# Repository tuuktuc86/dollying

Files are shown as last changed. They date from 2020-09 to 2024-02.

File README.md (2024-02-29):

# Dollying (휴대폰 어플리케이션과 연동 가능한 영상 촬영 장비)

## 작품개요
### 개발배경
대한민국 기준, 하루 평균 유튜브 시청 시간은 58.8분으로 다른 프로그램에 비해 사용 시간면에서 월등히 높다. 유튜브 영상 수요의 증가로 유튜브 영상 업로드 시간이 5년 사이에 약 10배 증가하였으며, 업로드 되는 영상 중 42%는 People 카테고리로 Vlog와 같은 개인의 일상에 관련되는 내용을 담고 있다. 이러한 1인 영상 매체가 성장하며 개인 방송장비 매출도 2년 사이에 540% 증가하였다.

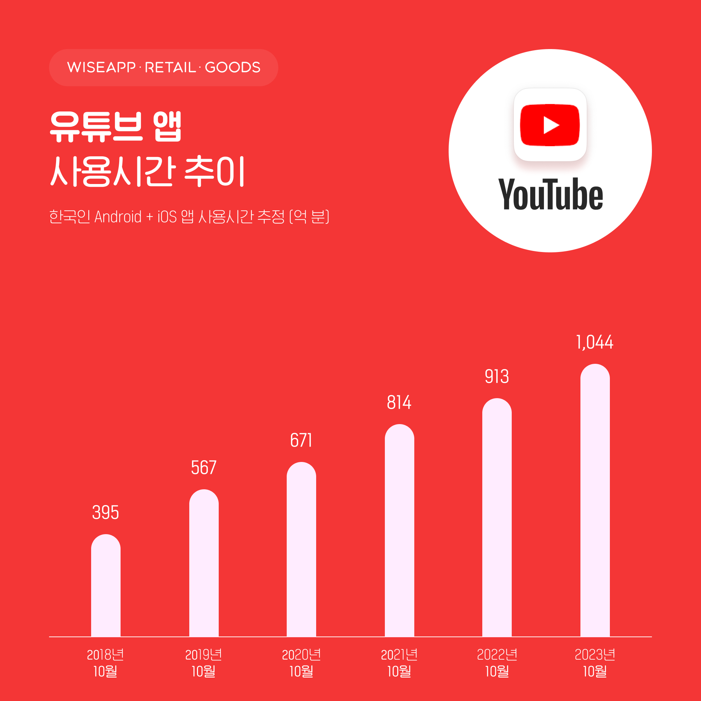
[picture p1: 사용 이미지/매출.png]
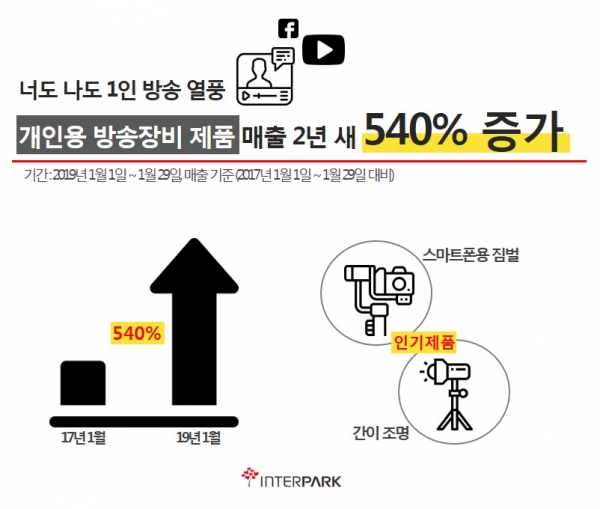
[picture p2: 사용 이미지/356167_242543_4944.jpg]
 

### 전동달리
영화 촬영 시 사용하는 장비를 최근 소형화, 전동화 시켜서 1인 영상 촬영에 사용되고 있다. 현재 시중에 사용되는 제품은 움직임 설정에 정교함이 없기 때문에 휴대폰 어플을 통해서 섬세한 제어와 다양한 움직임을 가능하게 하는 전동달리 제작을 목표로 하였다.

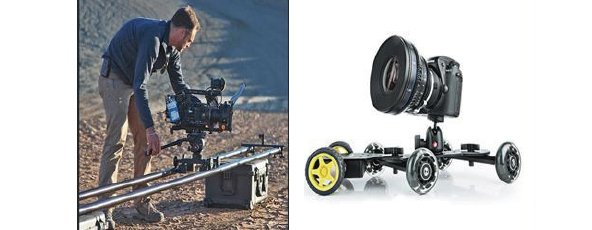
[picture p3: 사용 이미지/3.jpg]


## 작품 설명
### 주요 동작 및 특징
외관
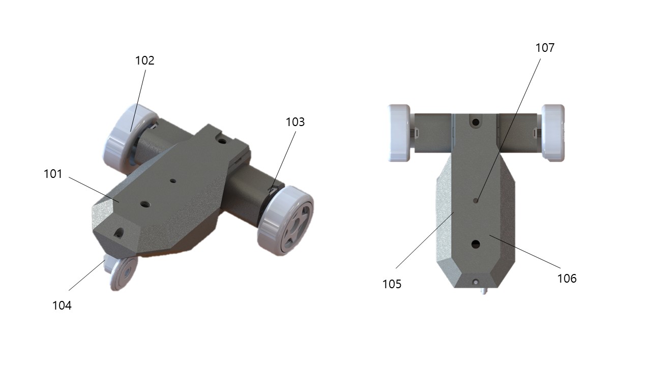
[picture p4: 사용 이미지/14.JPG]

- 앞바퀴는 방향을, 뒷바퀴는 전진과 후진 기능을 수행한다.<br/>
- 윗면의 구멍으로 카메라를 고정한다.<br/>

애플리케이션 설명 : UI 디자인
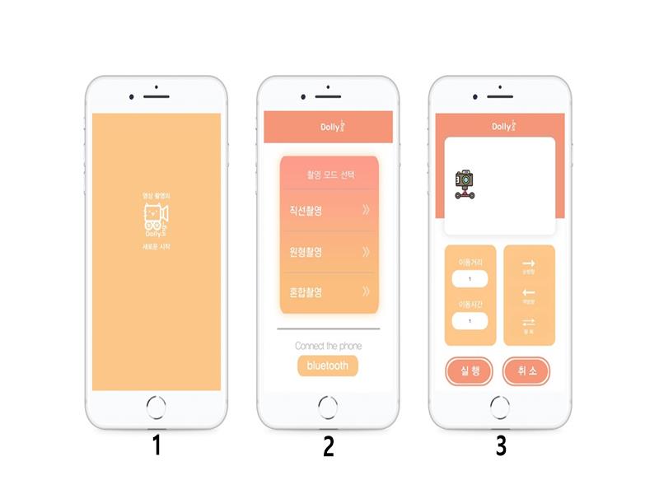
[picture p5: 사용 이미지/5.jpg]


1. 애플리케이션 시작 화면이다.<br/>
2. 메뉴화면으로 블루투스 연결과 모드선택(직선 촬영, 원형 촬영, 혼합 촬영)이 가능하다.<br/>
3. 직선 촬영 모드 > 이동거리와 이동시간을 입력할 수 있고 기능(순방향, 역방향, 왕복)을 설정이 가능하다<br/>
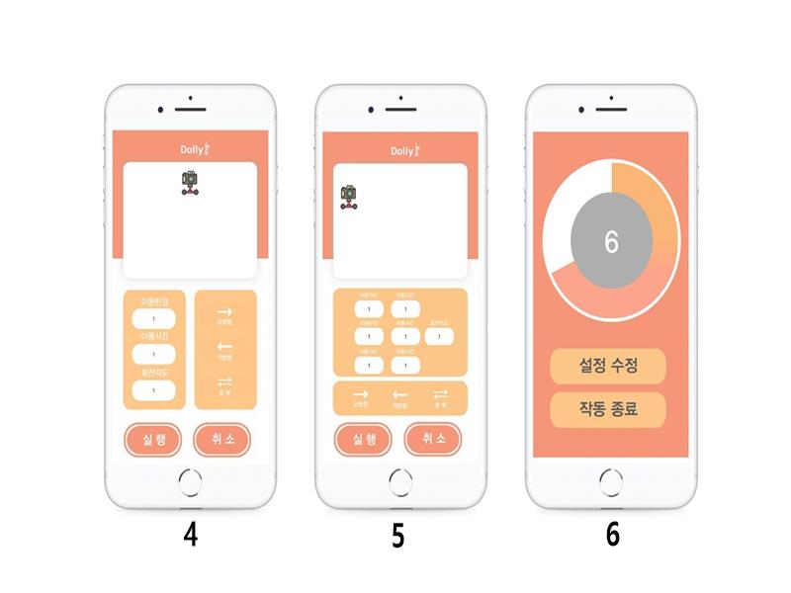
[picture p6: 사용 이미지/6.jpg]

4. 원형 촬영 모드 > 이동반경, 이동시간, 회전각도를 입력 할 수 있고 기능(순방향, 역방향, 왕복)을 설정 가능, 이동반경은 회전 반지름을, 회전각도는 원형으로 회전하는 각도를 의미한다.<br/>
5. 혼합 촬영 모드 > 직선촬영모드와 원형 촬영 모드를 합친 모드로 직선운동1-원형운동-직선운동2 구조로 구성, 직선운동 1,2구간의 이동거리와 이동시간과 원형운동의 이동반경, 이동시간, 회전 각도를 입력 할 수 있다. 또한 기능(순방향, 역방향, 왕복)을 설정이 가능하다.<br/>
6. 각 모드에서 실행을 눌렀을 때 넘어가는 화면. 기기 작동 시간이 종료되는 시간을 나타내며 입력 값은 수정이 가능하다.<br/>

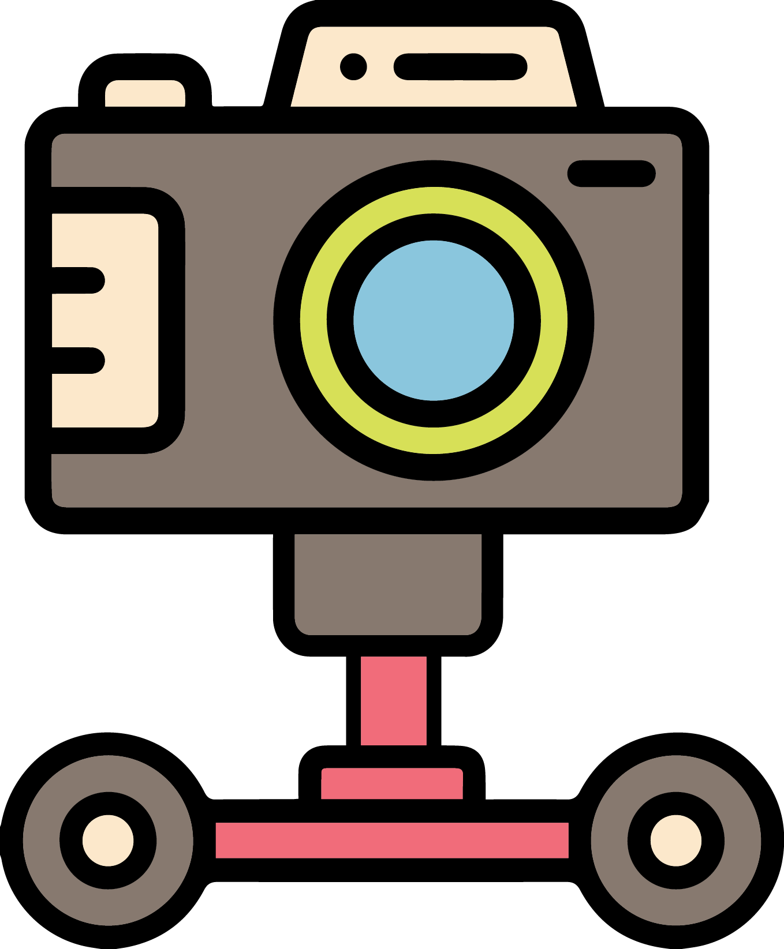
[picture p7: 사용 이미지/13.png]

③,④,⑤번 상단의 전동 달리 그림은 설정 값에 따라 움직이며 사용자가 기기 실행 전 움직임을 알 수 있도록 도와준다.<br/>
⑥번 상단의 숫자는 기기가 움직이는데 걸리는 시간을 알려주며 시간이 지나면서 감소한다.<br/>

### 전체 시스템 구성
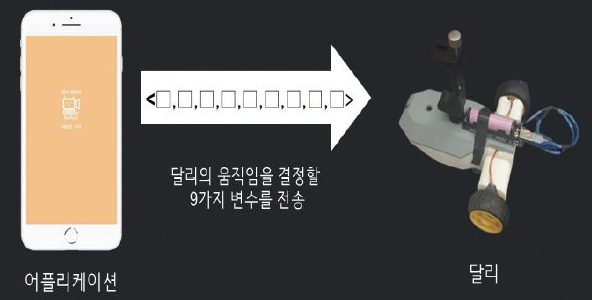
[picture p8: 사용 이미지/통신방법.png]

<> 전송의 시작과 끝을 나타내는 구분자  <br/>
① 촬영 모드(직선 촬영, 원형 촬영, 혼합 촬영)를 결정하는 변수  <br/>
② 직선 촬영 모드 시 이동거리 변수, 혼합 촬영 모드 시 직선운동 1구간의 이동거리 변수 <br/> 
③ 직선 촬영 모드 시 이동시간 변수, 혼합 촬영 모드 시 직선운동 1구간의 이동시간 변수  <br/>
④ 원형 촬영 모드 시 이동반경 변수, 혼합 촬영 모드 시 원형운동의 이동반경 변수  <br/>
⑤ 원형 촬영 모드 시 이동시간 변수, 혼합 촬영 모드 시 원형운동의 이동시간 변수  <br/>
⑥ 원형 촬영 모드 시 회전각도 변수, 혼합촬영모드 시 원형운동의 회전각도 변수  <br/>
⑦ 혼합 촬영 모드 시 직선운동 2구간의 이동거리 변수  <br/>
⑧ 혼합 촬영 모드 시 직선운동 2구간의 이동시간 변수  <br/>
⑨ 기능(순방향, 역방향, 왕복)을 나타내는 변수  <br/>

### 개발 환경(개발 언어, Tool, 사용 시스템 등)
전동 달리 코딩 : C,C++, Arduiono<br/>
애플리케이션 개발 : C#, Unity<br/>
전동 달리 모델링 : SOLIDWORKS<br/>
어플, 로고 디자인 : Adobe Photoshop,Adobe Illustrator<br/>

## 단계별 제작 과정
·  0 단계: 아이디어 선정<br/>
·  1 단계: UI디자인 구성, 전동달리 구조 확정, 사용 부품 선정<br/>
·  2 단계: 전동달리 코딩 개발, 애플리케이션 개발, 전동달리 모델링 및 3D프린터 출력<br/>
·  3 단계: 3D프린터 파트 조립, 기기 시험 작동 후 코드 수정<br/>

### 0단계 : 아이디어 선정
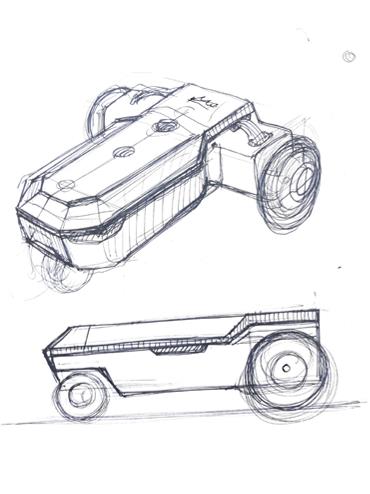
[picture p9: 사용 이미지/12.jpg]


### 1단계 : 어플 디자인 및 부품 구성
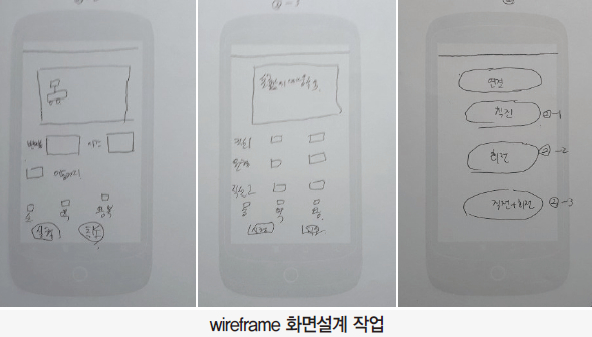
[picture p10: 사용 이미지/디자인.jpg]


사용부품 선정
· 아두이노 우노 x 1ea
· 아두이노 우노 쉴드 x 1ea
· 스텝모터, 모터 드라이버 x 2ea
· 서보모터 x 1ea
· 배터리 x 1ea
· 배터리 충전 모듈 x 1ea
· 바퀴 x 2ea

### 2단계 : 전동달리 모델링 및 3D프린터 출력


전동달리 코드 개발 : github 참고
어플리케이션 개발 : github 참고

### 3단계 : 3D프린터 파트 조립
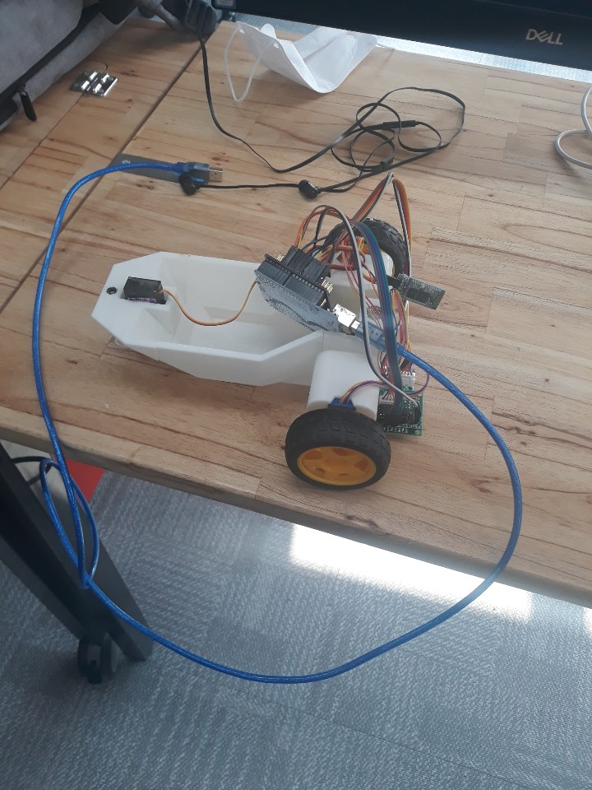
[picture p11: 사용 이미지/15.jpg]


기기 시험 작동 후 코드 수정
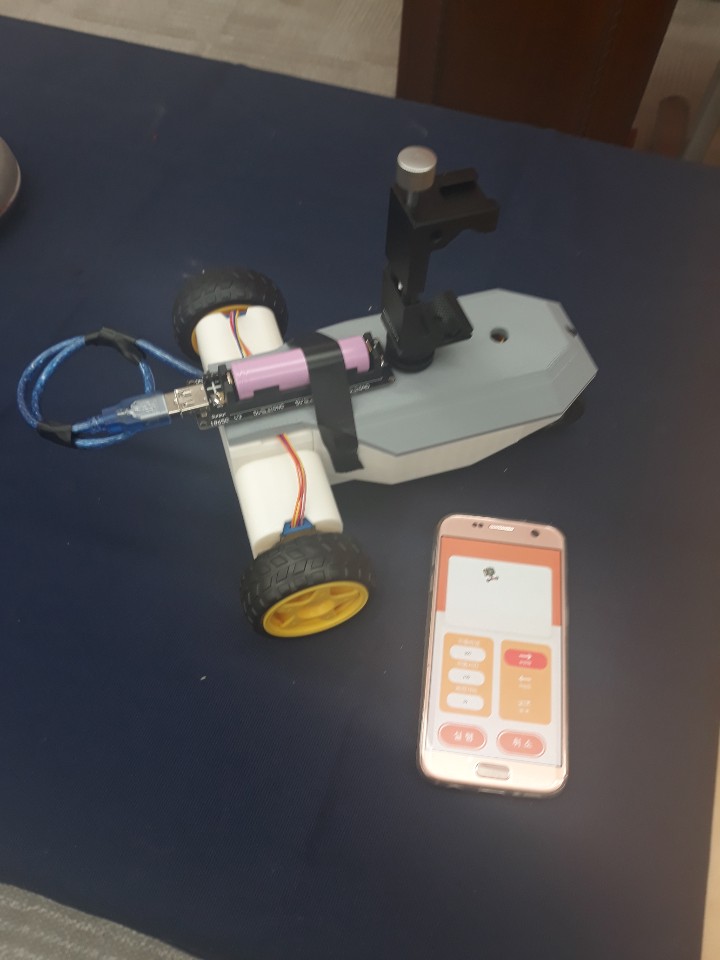
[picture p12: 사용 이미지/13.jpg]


## 기타

### 회로도
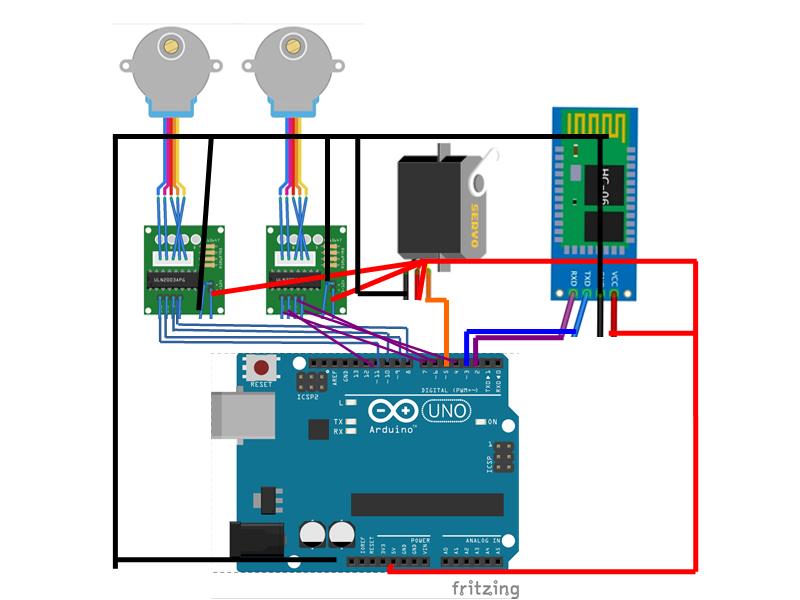
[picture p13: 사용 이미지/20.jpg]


### 플레이스토어 등록
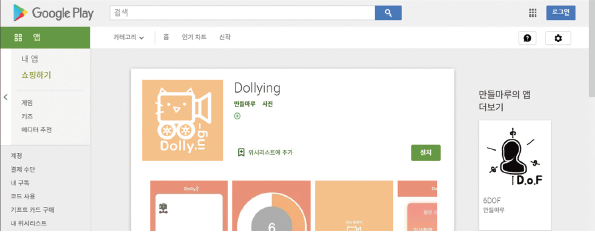
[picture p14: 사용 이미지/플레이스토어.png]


### 계산 과정
스텝 모터가 움직이는 데 필요한 값 계산
계산을 시작하기 전에 알아야 하는 값

1. 스텝모터가 1회전이 몇 개의 스텝으로 이루어져 있는지 여부
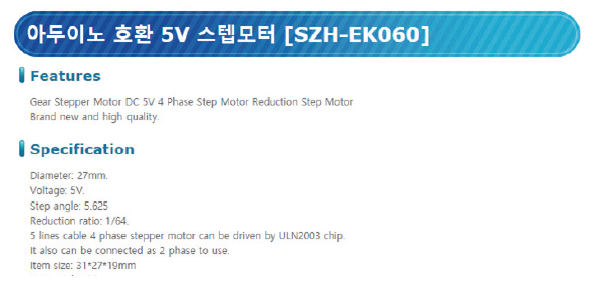
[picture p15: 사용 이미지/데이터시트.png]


2. 바퀴 반지름.
· 왼쪽 모터의 1회전에 필요한 스텝은 8이다.
· 디바이스마트에 나와있는 스텝모터 (SZH-EK060) 사양

Step angle이 5.425。이고 감속비는 1/64이므로 1스텝 0.084765625。당 회전한다. 360÷0.084765625 ≒4247이지만 모터드라이버의 full step모드에서는 1/2한 근사치인 2048을 이용한다.

애플리케이션에서 전송받는 값
1. 기기의 이동거리, 2. 기기 이동에 걸리는 시간

구해야 하는 값
1. 스텝모터의 회전속도는 rpm단위이기 때문에 위의 값들을 활용하여 rpm값을 구해야 한다.
2. 해당 거리만큼 이동하는 데 필요한 스텝 수를 알아야 한다.

회전에 필요한 스텝 수 구하기
1. 바퀴의 원주를 알아야 하므로 2πr(r은 반지름)을 통해서 원주를 알아낸다.
2. 이동 거리를 원주로 나누어 바퀴의 회전수를 구한다.
3. 회전수에 스텝 모터 한바퀴 스텝을 곱하여(이번 프로젝트에 사용한 스텝모터의 1회전에 필요한 스텝은 2048) 이동에 필요한 스텝을 알 수 있다.

회전속도 구하기
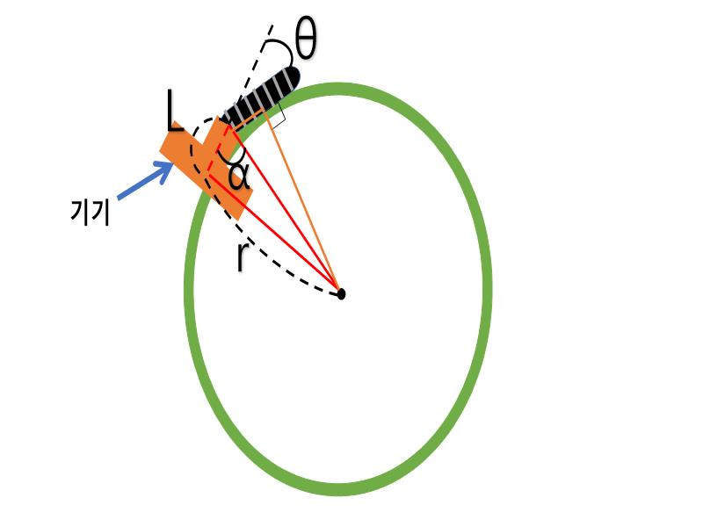
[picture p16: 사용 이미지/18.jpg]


1. rpm = 회전수 * 이동시간 / 60.

2. 회전 반지름에 따른 회전 각도 구하기
r= 회전 반지름
L= 기기 길이
α=  arctan(r/L)

빨간 삼각형과 주황 삼각형은 합동이므로 θ=180-2α이다.


http://www.ntrexgo.com/archives/39953

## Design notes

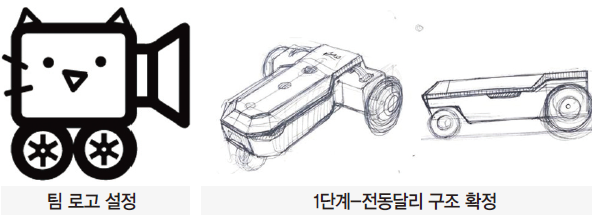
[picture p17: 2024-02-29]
사용 이미지/디자인2.png

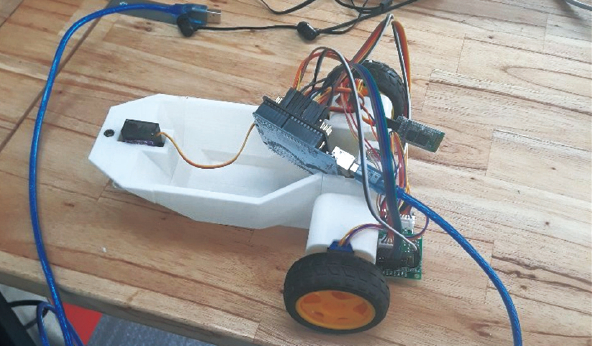
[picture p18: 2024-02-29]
사용 이미지/사진2.jpg

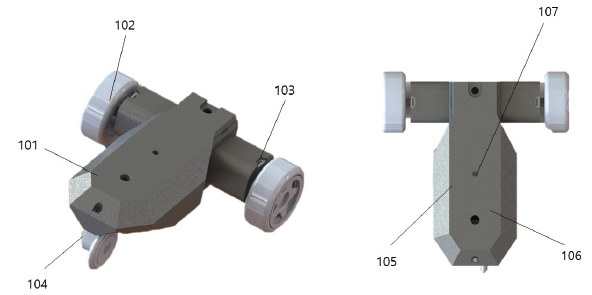
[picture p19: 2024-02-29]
사용 이미지/외형.jpg

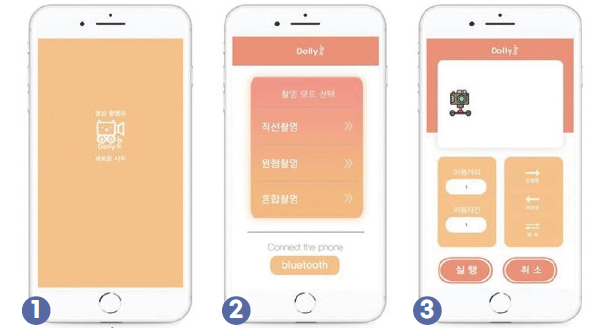
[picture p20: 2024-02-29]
사용 이미지/어플2.png

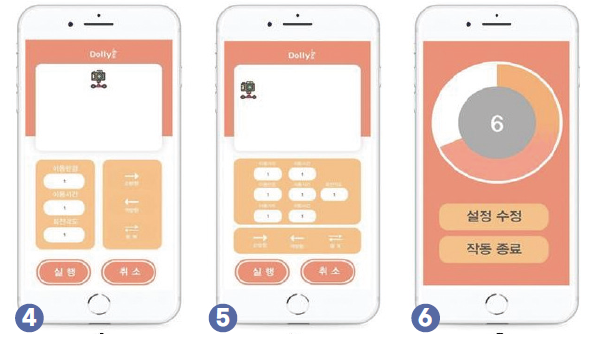
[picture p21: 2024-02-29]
사용 이미지/어플1.png

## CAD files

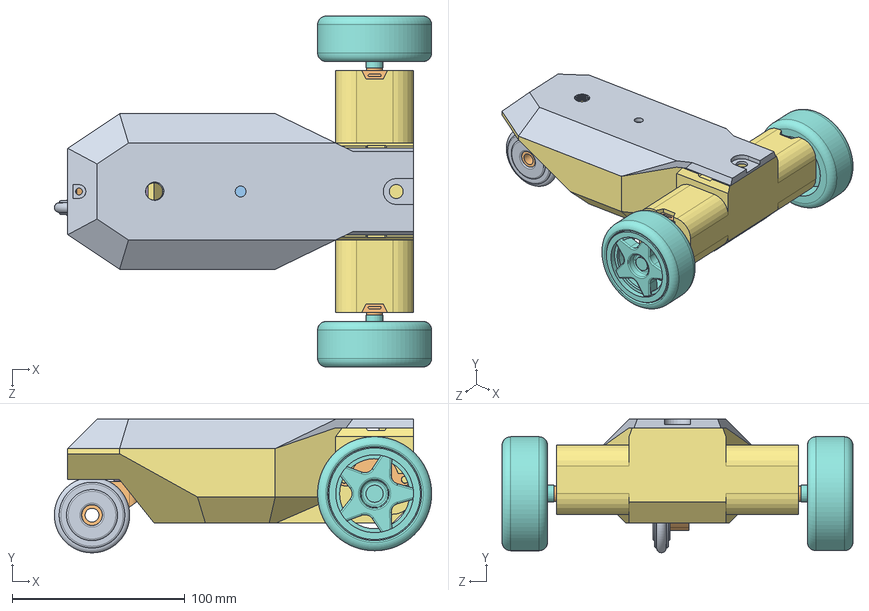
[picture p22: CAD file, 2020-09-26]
어셈블리1.SLDASM
218.2 x 77.3 x 203.0 mm
상단
바퀴모터 x 2
아두이노
건전지
모터드라이버 x 2
서보(조향)
하단
뒷바퀴 x 2
앞바꾸2
조향

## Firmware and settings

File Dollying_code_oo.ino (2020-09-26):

//헤더파일
#include <Servo.h>
#include <SoftwareSerial.h>
#include <Stepper.h>

//스테핑모터 정보. 모터 스펙에 맞게 설정
const int stepsPerRevolution = 2048; //28BYJ-48는 1회전당 2048스텝

//핀번호
#define BT_RXD 2
#define BT_TXD 3
Stepper rightStepper(stepsPerRevolution, 11, 9, 10, 8);  //오른쪽 바퀴를 돌릴 모터
Stepper leftStepper(stepsPerRevolution, 7, 12, 6, 4);    //왼쪽 바퀴를 돌릴 모터
int servoPin = 5;                                        // PWM 핀인 ~표시가 있는 핀에 연결


//블루투스 설정
SoftwareSerial BTSerial(BT_RXD, BT_TXD); // change this to fit the number of steps per revolution

//data 읽기 시작, 종료 상태 변수
bool isStart = false;   // 읽기 시작
bool isEnd = false;     // 읽기 종료
String resultStr = "";  // 최종 Data를 저장할 문자열

//불루투스에서 받은 값을 나눠서 넣을 값.
int sep = 0;            //직선, 원형, 혼합 운동을 결정하는 변수
int dis1 = 0;           //직선 운동의 거리 변수, 혼합 운동의 1번 직선 구간 거리 변수
int tim1 = 0;           //직선 운동의 시간 변수, 혼합 운동의 1번 직선 구간 시간 변수
int rad2 = 0;           //원형 운동의 반지름 변수, 혼합 운동의 회전 구간의 반지름 변수
int tim2 = 0;           //원형 운동의 시간 변수, 혼합 운동의 회전 구간의 시간 변수
int ang2 = 0;           //원형 운동의 각도 변수, 혼합 운동의 회전 구간의 각도 변수
int dis3 = 0;           //혼합 운동의 2번 직선 구간 거리 변수
int tim3 = 0;           //혼합 운동의 2번 직선 구간 시간 변수
int mod = 0;            //직진, 후진, 왕복 기능을 결정하는 변수

//서브모터 설정
Servo servo;           // Servo 클래스로 servo 객체 생성
int angle = 0;         // Servo 모터의 각도 (0~180)
int stAngle = 82;      //Servo 모터 직진용 각도, 82도가 직진, 사용하기 전에 기기마다 맞는 설정값을 입력해줘야 함
double ccAngle = 0;    // 원형 운동시 서브모터 각도, 어플에서 넘어온 값으로 변경됨
int tnAngle = 0;       // 혼합 운동시 서브모터 각도, 어플에서 넘어온 값으로 변경됨

//바퀴 데이터
int wheelRadius = 3;                            //바퀴 반지름
float wheelCircum = wheelRadius * 2 * 3.141592; // 바퀴 원주


//직선 운동시 필요 데이터를 계산하기 위한 변수
float stTurnNum = 0;              //회전수
float stStepPerRevolution = 0;    //step per revolution
float stSpeedNeed = 0;            //회전속도(rpm)을 구하기 위해 필요한 변수
float stStepSpeed = 0;            //회전속도(rpm)

//원형 운동시 필요 데이터를 계산하기 위한 변수
float ccTurnNum = 0;            //회전수
float ccDis = 0;                //회전 이동거리
float ccStepPerRevolution = 0;  //step per revolution
float ccSpeedNeed = 0;          //회전속도(rpm)을 구하기 위해 필요한 변수
float ccStepSpeed = 0;          //회전속도(rpm)

//직선 운동3에 필요한 데이터를 계산하기 위한 변수
int stTurnNum3 = 0;             //회전수
int stStepPerRevolution3 = 0;   //step per revolution
int stSpeedNeed3 = 0;           //회전속도(rpm)을 구하기 위해 필요한 변수
int stStepSpeed3 = 0;           //회전속도(rpm)

//몸체 데이터
float bodylength = 10; // 몸체 세로 길이. 회전각을 구할 때에 필요

//,를 찾아내기 위한 변수
int first = 0;
int second = 0;
int third = 0;
int fourth = 0;
int fifth = 0;
int sixth = 0;
int seventh = 0;
int eighth = 0;

//회전에 필요한 데이터
int turnAngle = 0;
float turnData = 0;

void setup() {
  //통신 설정
  Serial.begin(9600);     //컴퓨터와의 통신속도 설정
  BTSerial.begin(9600);   //블루투스와의 통신속도 설정

  //Servo 모터 핀 설정
  servo.attach(servoPin); //servoPin 데이터는 위에 표기
}

void loop() {

  if (BTSerial.available()) {
    while (1) {
      char val = BTSerial.read();   //블루투스 데이터를 받아와 val변수에 삽입

      //데이터 읽기 시작
      if (val == '<') {
        Serial.println("start");
        resultStr = ""; // 최종 Data 문자열 초기화
        isStart = true;
        isEnd = false;
        continue;   // while문으로 바로 이동
      }
      // 데이터 읽기 종료
      else if (val == '>') {
        Serial.println("end");
        isEnd = true;
        break;
      }
      // 중간 데이터값을 최종 Data 문자열에 추가
      else {
        resultStr = String(resultStr + val);
      }
    }

    //시작 부호와 종료 부호가 들어왔다면
    if (isStart == true && isEnd == true) {
      Serial.print("전송된 데이터 : ");
      Serial.println(resultStr);

      //컴마 기호 파악
      first = resultStr.indexOf(",");
      second = resultStr.indexOf(",", first + 1);
      third = resultStr.indexOf(",", second + 1);
      fourth = resultStr.indexOf(",", third + 1);
      fifth = resultStr.indexOf(",", fourth + 1);
      sixth = resultStr.indexOf(",", fifth + 1);
      seventh = resultStr.indexOf(",", sixth + 1);
      eighth = resultStr.indexOf(",", seventh + 1);
    }

    //컴마 위치를 파악하고 싶을 때 아래 주석을 해제하세요
    /*
      Serial.print("first : ");
      Serial.println(first);
      Serial.print("second : ");
      Serial.println(second);
      Serial.print("third : ");
      Serial.println(third);
      Serial.print("fourth : ");
      Serial.println(fourth);
      Serial.print("fifth : ");
      Serial.println(fifth);
      Serial.print("sixth : ");
      Serial.println(sixth);
      Serial.print("seventh : ");
      Serial.println(seventh);
      Serial.print("eighth : ");
      Serial.println(eighth);
      Serial.print("length : ");
      Serial.println(strlength);
    */

    //문자열 나누기
    String sepS = resultStr.substring(0, first);              //직선, 원형, 회전 중 어떤 것인지 알려주는 데이터
    String dis1S = resultStr.substring(first + 1, second);    //직선 운동에 필요한 거리 값
    String tim1S = resultStr.substring(second + 1, third);    //직선 운동에 필요한 시간 값
    String rad2S = resultStr.substring(third + 1, fourth);    //원형 운동에 필요한 반지름 값
    String tim2S = resultStr.substring(fourth + 1, fifth);    //원형 운동에 필요한 시간 값
    String ang2S = resultStr.substring(fifth + 1, sixth);      //원형 운동에 필요한 각도 값
    String dis3S = resultStr.substring(sixth + 1, seventh);    //회전 운동에 필요한 2번째 직선운동 거리 값
    String tim3S = resultStr.substring(seventh + 1, eighth);    //회전 운동에 필요한 2번째 직선운동 시간 값
    String modS = resultStr.substring(eighth + 1);              //직진, 후진, 왕복 중 어떤 것인지 알려주는 데이터

    //문자열을 int형 인자로 변환
    sep = sepS.toInt();
    dis1 = dis1S.toInt();
    tim1 = tim1S.toInt();
    rad2 = rad2S.toInt();
    tim2 = tim2S.toInt();
    ang2 = ang2S.toInt();
    dis3 = dis3S.toInt();
    tim3 = tim3S.toInt();
    mod = modS.toInt();

    //잘라낸 값들이 잘 들어갔나 확인하려면 주석을 해제하세요
    /*
      Serial.print("seperate : ");
      Serial.println(sep);
      Serial.print("distance1 : ");
      Serial.println(dis1);
      Serial.print("time1 : ");
      Serial.println(tim1);
      Serial.print("radius2 : ");
      Serial.println(rad2);
      Serial.print("time2 : ");
      Serial.println(tim2);
      Serial.print("angle2 : ");
      Serial.println(ang2);
      Serial.print("distance3 : ");
      Serial.println(dis3);
      Serial.print("time3 : ");
      Serial.println(tim3);
      Serial.print("mode : ");
      Serial.println(mod);
    */

    //다음 불루투스 값을 받아들이기 위한 변수 초기화
    isStart = false;
    isEnd = false;

    //직선 운동
    if (sep == 2) {
      //Serial.println("직선 운동 모드로 설정되었습니다.");

      //직선운동에서 서브모터 각도 수정
      servo.write(stAngle);    //변수 값으로 고정했습니다. 장치 개발 후 수정이 필요합니다.
      delay(500);              //서브모터가 돌고 바로 스텝모터가 도는 것을 방지하기 위해 잠깐의 텀을 둡니다.

      //직선운동 스텝모터 작동에 필요한 값 계산
      stTurnNum = (float)dis1 / wheelCircum;           //회전수
      stSpeedNeed = stTurnNum * 60;                    //계산과정 추후에 정리
      stStepPerRevolution = (float)stTurnNum * stepsPerRevolution;    //모터 한바퀴가 2048step이기 때문에 stepsPerRevolution을 곱함
      stStepSpeed = (float)stSpeedNeed / tim1;         //회전속도(rpm)

      //회전수, step per revolution, 회전속도(rpm)을 확인하려면 주석을 해제하세요
      /*
        Serial.print("직진 운동에서의 회전수 : ");
        Serial.println(stTurnNum);
        Serial.print("직진 운동에서의 step per revolution : ");
        Serial.println(stStepPerRevolution);
        Serial.print("직진 운동에서의 회전속도(rpm) : ");
        Serial.println(stStepSpeed);
      */

      //직진모드
      if (mod == 0) {
        //Serial.println("직선운동의 직진모드가 시작되었습니다.");
        goForward(stStepSpeed, stStepPerRevolution);
      }

      //후진모드
      else if (mod == 1) {
        //Serial.println("직선운동의 후진모드가 시작되었습니다.")
        goBackward(stStepSpeed, stStepPerRevolution);
      }

      //왕복모드
      else if (mod == 2) {
        //Serial.println("직선운동의 왕복모드가 시작되었습니다.");
        goForward(stStepSpeed, stStepPerRevolution);
        goBackward(stStepSpeed, stStepPerRevolution);
      }
    }

    //원형 운동
    else if (sep == 3) {

      //Serial.println("원형 운동 모드로 설정되었습니다.");

      // 서보모터 회전각도 계산
      // 계산과정은 나중에 따로 정리하겠습니다. 
      turnData = (float)rad2 / bodylength;
      ccAngle = 180 - 2 * atan(turnData);

      //서보모터 회전
      servo.write(ccAngle);     //서보모터 각도 설정
      delay(500);               //서브모터가 돌고 바로 스텝모터가 도는 것을 방지하기 위해 잠깐의 텀을 둡니다.

      //스텝모터 관련 계산
      ccDis = (float)0.01756 * ang2 * rad2;           //회전 이동거리
      ccTurnNum = (float)ccDis / wheelCircum;        //회전수. 회전수는 이동거리 나누기 바퀴 원주
      ccStepPerRevolution = (float)ccTurnNum * stepsPerRevolution;   //step per revolution
      ccSpeedNeed = ccTurnNum * 60;                  //회전속도(rpm)을 구하기 위해 필요한 변수
      ccStepSpeed = (float)ccSpeedNeed / tim2;        //회전속도(rpm)

      //회전 이동거리, 회전수, step per revolution, 회전속도를 확인하려면 주석을 해제하세요.
      /*
        Serial.print("회전이동거리 : ");
        Serial.println(ccDis);
        Serial.print("회전수");
        Serial.println(ccTurnNum);
        Serial.print("step per revolution : ");
        Serial.println(ccStepPerRevolution);
        Serial.print("회전속도 : ");
        Serial.println(ccStepSpeed);
      */

      //직진모드
      if (mod == 0) {
        //Serial.println("원형운동의 직진모드가 시작되었습니다.");
        goForward(stStepSpeed, stStepPerRevolution);
      }

      //후진모드
      else if (mod == 1) {
        //Serial.println("원형운동의 후진모드가 시작되었습니다.");
        goBackward(stStepSpeed, stStepPerRevolution);
      }

      //왕복모드
      else if (mod == 2) {
        //Serial.println("원형운동의 왕복모드가 시작되었습니다.");
        goForward(stStepSpeed, stStepPerRevolution);
        goBackward(stStepSpeed, stStepPerRevolution);
      }
    }

    //회전운동 모드
    else if (sep == 4) {

      //직선운동1 스텝모터 작동에 필요한 값 계산
      stTurnNum = (float)dis1 / wheelCircum;        //회전수
      stSpeedNeed = stTurnNum * 60;                //계산과정 추후에 정리
      stStepPerRevolution = (float)stTurnNum * stepsPerRevolution; //모터 한바퀴가 2048step이기 때문에 stepsPerRevolution을 곱함
      stStepSpeed = (float)stSpeedNeed / tim1;      //회전속도(rpm)

      //회전수, step per revolution, 회전속도(rpm)을 확인하려면 주석을 해제하세요
      /*
        Serial.print("직진 운동1에서의 회전수 : ");
        Serial.println(stTurnnum);
        Serial.print("직진 운동1에서의 step per revolution : ");
        Serial.println(stStepPerRevolution);
        Serial.print("직진 운동1에서의 회전속도(rpm) : ");
        Serial.println(stStepSpeed);
      */

      //스텝모터 회전 관련 계산
      ccDis = (float)0.01756 * ang2 * rad2;           //회전 이동거리
      ccTurnNum = (float)ccDis / wheelCircum;        //회전수. 회전수는 이동거리 나누기 바퀴 원주
      ccStepPerRevolution = (float)ccTurnNum * stepsPerRevolution;   //step per revolution
      ccSpeedNeed = ccTurnNum * 60;                  //회전속도(rpm)을 구하기 위해 필요한 변수
      ccStepSpeed = (float)ccSpeedNeed / tim2;        //회전속도(rpm)

      //회전 이동거리, 회전수, step per revolution, 회전속도를 확인하려면 주석을 해제하세요.
      /*
        Serial.print("회전이동거리 : ");
        Serial.println(ccDis);
        Serial.print("회전수");
        Serial.println(ccTurnNum);
        Serial.print("step per revolution : ");
        Serial.println(ccStepPerRevolution);
        Serial.print("회전속도 : ");
        Serial.println(ccStepSpeed);
      */

      //직선운동3 스텝모터 작동에 필요한 값 계산
      stTurnNum3 = (float)dis3 / wheelCircum;        //회전수
      stSpeedNeed3 = stTurnNum * 60;                //계산과정 추후에 정리
      stStepPerRevolution3 = (float)stTurnNum * stepsPerRevolution; //모터 한바퀴가 2048step이기 때문에 stepsPerRevolution을 곱함
      stStepSpeed3 = (float)stSpeedNeed / tim3;      //회전속도(rpm)

      //회전수, step per revolution, 회전속도(rpm)을 확인하려면 주석을 해제하세요
      /*
        Serial.print("직진 운동3에서의 회전수 : ");
        Serial.println(stTurnnum3);
        Serial.print("직진 운동3에서의 step per revolution : ");
        Serial.println(stStepPerRevolution3);
        Serial.print("직진 운동3에서의 회전속도(rpm) : ");
        Serial.println(stStepSpeed3);
      */


      //직진모드
      if (mod == 0) {
        //Serial.println("회전 운동 직진모드로 설정되었습니다.");

        //직진1
        //직선운동에서 서브모터 각도 수정
        servo.write(stAngle);    //변수 값으로 고정했습니다. 장치 개발 후 수정이 필요합니다.
        delay(500);              //서브모터가 돌고 바로 스텝모터가 도는 것을 방지하기 위해 잠깐의 텀을 둡니다.

        //직선운동에서 스텝모터 움직임
        goForward(stStepSpeed, stStepPerRevolution);

        //회전
        // 계산과정은 나중에 따로 정리하겠습니다.
        turnData = (float)rad2 / bodylength;
        ccAngle = 180 - 2 * atan(turnData);

        //서보모터 회전
        for (int i = 0; i < ccAngle; i++) {
          turnAngle += 1;
          servo.write(turnAngle);     //서보모터 각도 설정
        }

        //스텝모터 관련 계산
        ccDis = (float)0.01756 * ang2 * rad2;           //회전 이동거리
        ccTurnNum = (float)ccDis / wheelCircum;        //회전수. 회전수는 이동거리 나누기 바퀴 원주
        ccStepPerRevolution = (float)ccTurnNum * stepsPerRevolution;   //step per revolution
        ccSpeedNeed = ccTurnNum * 60;                  //회전속도(rpm)을 구하기 위해 필요한 변수
        ccStepSpeed = (float)ccSpeedNeed / tim2;        //회전속도(rpm)

        goForward(ccStepSpeed, ccStepPerRevolution);

        // 직진3
        //직선운동에서 서브모터 각도 수정
        servo.write(stAngle);    //변수 값으로 고정했습니다. 장치 개발 후 수정이 필요합니다.
        delay(500);              //서브모터가 돌고 바로 스텝모터가 도는 것을 방지하기 위해 잠깐의 텀을 둡니다.

        goForward(stStepSpeed, stStepPerRevolution);
      }

      if (mod == 1) {
        //Serial.println("회전 운동 후진모드로 설정되었습니다.");
        //직진1
        //직선운동에서 서브모터 각도 수정
        servo.write(stAngle);    //변수 값으로 고정했습니다. 장치 개발 후 수정이 필요합니다.
        delay(500);              //서브모터가 돌고 바로 스텝모터가 도는 것을 방지하기 위해 잠깐의 텀을 둡니다.

        //직선운동에서 스텝모터 움직임
        goBackward(stStepSpeed, stStepPerRevolution);

        //회전
        //계산과정은 나중에 따로 정리하겠습니다.
        turnData = (float)rad2 / bodylength;
        ccAngle = 180 - 2 * atan(turnData);

        //서보모터 회전
        for (int i = ccAngle; i > 0; i--) {
          turnAngle -= 1;
          servo.write(turnAngle);     //서보모터 각도 설정
        }


        //스텝모터 관련 계산
        ccDis = (float)0.01756 * ang2 * rad2;           //회전 이동거리
        ccTurnNum = (float)ccDis / wheelCircum;        //회전수. 회전수는 이동거리 나누기 바퀴 원주
        ccStepPerRevolution = (float)ccTurnNum * stepsPerRevolution;   //step per revolution
        ccSpeedNeed = ccTurnNum * 60;                  //회전속도(rpm)을 구하기 위해 필요한 변수
        ccStepSpeed = (float)ccSpeedNeed / tim2;        //회전속도(rpm)

        goBackward(ccStepSpeed, ccStepPerRevolution);

        // 직진3
        //직선운동에서 서브모터 각도 수정
        servo.write(stAngle);    //변수 값으로 고정했습니다. 장치 개발 후 수정이 필요합니다.
        delay(500);              //서브모터가 돌고 바로 스텝모터가 도는 것을 방지하기 위해 잠깐의 텀을 둡니다.

        goBackward(stStepSpeed, stStepPerRevolution);
      }

      else if (mod == 2) {
        //Serial.println("회전 운동 왕복모드 직진부로 설정되었습니다.");

        //직진1
        //직선운동에서 서브모터 각도 수정
        servo.write(stAngle);    //변수 값으로 고정했습니다. 장치 개발 후 수정이 필요합니다.
        delay(500);              //서브모터가 돌고 바로 스텝모터가 도는 것을 방지하기 위해 잠깐의 텀을 둡니다.

        //직선운동에서 스텝모터 움직임
        goForward(stStepSpeed, stStepPerRevolution);

        //회전
        // 계산과정은 나중에 따로 정리하겠습니다.
        turnData = (float)rad2 / bodylength;
        ccAngle = 180 - 2 * atan(turnData);

        //서보모터 회전
        for (int i = 0; i < ccAngle; i++) {
          turnAngle += 1;
          servo.write(turnAngle);     //서보모터 각도 설정
        }

        //스텝모터 관련 계산
        ccDis = (float)0.01756 * ang2 * rad2;           //회전 이동거리
        ccTurnNum = (float)ccDis / wheelCircum;        //회전수. 회전수는 이동거리 나누기 바퀴 원주
        ccStepPerRevolution = (float)ccTurnNum * stepsPerRevolution;   //step per revolution
        ccSpeedNeed = ccTurnNum * 60;                  //회전속도(rpm)을 구하기 위해 필요한 변수
        ccStepSpeed = (float)ccSpeedNeed / tim2;        //회전속도(rpm)

        goForward(ccStepSpeed, ccStepPerRevolution);

        // 직진3
        //직선운동에서 서브모터 각도 수정
        servo.write(stAngle);    //변수 값으로 고정했습니다. 장치 개발 후 수정이 필요합니다.
        delay(500);              //서브모터가 돌고 바로 스텝모터가 도는 것을 방지하기 위해 잠깐의 텀을 둡니다.

        goForward(stStepSpeed, stStepPerRevolution);

        //Serial.println("회전 운동 왕복모드 후진부로 설정되었습니다.");
        //직진1
        //직선운동에서 서브모터 각도 수정
        servo.write(stAngle);    //변수 값으로 고정했습니다. 장치 개발 후 수정이 필요합니다.
        delay(500);              //서브모터가 돌고 바로 스텝모터가 도는 것을 방지하기 위해 잠깐의 텀을 둡니다.

        //직선운동에서 스텝모터 움직임
        goBackward(stStepSpeed, stStepPerRevolution);

        //회전
        // 계산과정은 나중에 따로 정리하겠습니다.
        turnData = (float)rad2 / bodylength;
        ccAngle = 180 - 2 * atan(turnData);

        //서보모터 회전
        for (int i = ccAngle; i > 0; i--) {
          turnAngle -= 1;
        }
        servo.write(turnAngle);     //서보모터 각도 설정

        //스텝모터 관련 계산
        ccDis = (float)0.01756 * ang2 * rad2;           //회전 이동거리
        ccTurnNum = (float)ccDis / wheelCircum;        //회전수. 회전수는 이동거리 나누기 바퀴 원주
        ccStepPerRevolution = (float)ccTurnNum * stepsPerRevolution;   //step per revolution
        ccSpeedNeed = ccTurnNum * 60;                  //회전속도(rpm)을 구하기 위해 필요한 변수
        ccStepSpeed = (float)ccSpeedNeed / tim2;        //회전속도(rpm)

        goBackward(stStepSpeed, stStepPerRevolution);

        // 직진3
        //직선운동에서 서브모터 각도 수정
        servo.write(stAngle);    //변수 값으로 고정했습니다. 장치 개발 후 수정이 필요합니다.
        delay(500);              //서브모터가 돌고 바로 스텝모터가 도는 것을 방지하기 위해 잠깐의 텀을 둡니다.

        goBackward(stStepSpeed, stStepPerRevolution);

      }


    }
    //변수초기화 혹시 몰라서 넣어봅니다.
    turnAngle = 0;
  }
}
void goForward(float a, int b) {
  rightStepper.setSpeed(a);
  leftStepper.setSpeed(a);
  for (int i = 0; i < b; i++) {
    rightStepper.step(1);
    leftStepper.step(-1);
  }
}

void goBackward(float c, int d) {
  rightStepper.setSpeed(c);
  leftStepper.setSpeed(c);
  for (int i = 0; i < d; i++) {
    rightStepper.step(-1);
    leftStepper.step(1);
  }
}

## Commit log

2020-09-26 리드미파일 커밋
2020-09-26 main file
    [어셈블리1.SLDASM]
